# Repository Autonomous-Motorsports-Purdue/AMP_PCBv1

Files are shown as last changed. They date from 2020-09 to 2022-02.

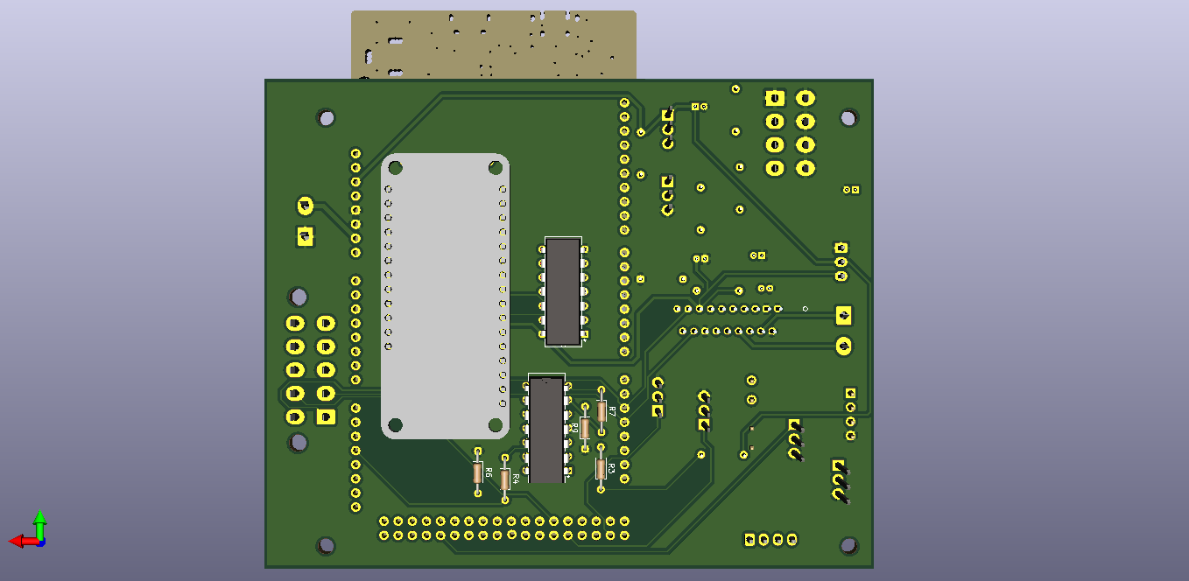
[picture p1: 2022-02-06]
PDF/PCB_2020_back.png

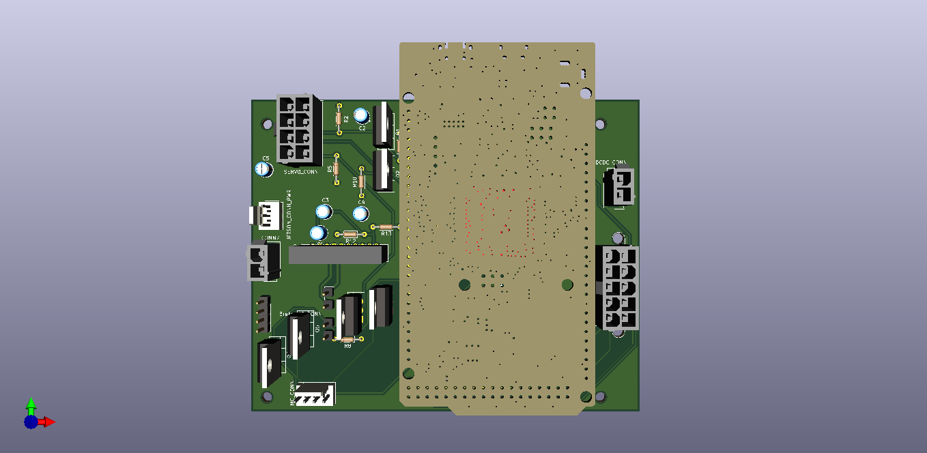
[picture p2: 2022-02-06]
PDF/PCB_2020.png

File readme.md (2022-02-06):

PCB Documentation

	- H-bridge
		- An H-bridge is made up of four MOSFETs and four diodes.
		- It switches motor direction based on which two MOSFETs are on.
		- The diodes serve to allow reverse current from the motor to be released.
		- The current solution is Adafruit DRV8871.
			- Its current Limit is 3.6 Amps.
			- This is not enough for the brake Linear Actuator.
		- Recommend switching from DRV8871 to MCP1407.
		- Has peak current capability of 6 A, which is enough for the braking actuator.
		- https://ww1.microchip.com/downloads/en/DeviceDoc/20002019C.pdf
			
	- Steering PWM
		- A square wave is sent to input A of the servo.
		- The pulse width determines position of servo.
		
	- Differential Amplifier 
		- 
		- The formula for a voltage divider is V = VR + (R3/R1)(V1 - V2).
		- The circuit amplifies the difference between the two inputs and adds the voltage VR as an offset.
		- Amplifier for PCB needs to change 0.55 V to 0 V, and  2.75 to 12 volts.
		- Diagram for Reference: https://www.electronicshub.org/wp-content/uploads/2015/01/1.-Differential-amplifier-circuit.jpg
		
	- Braking Linear Actuator
		- 5 Amp Max Current Draw at 12 Volts
		- Duty Cycle: 5 minutes on, 15 minutes off
		- Speed of 1.38 in/s with load of 35 lbs

		Changes
			-C1, C3, C4 backwards footprints (non-polarized capacitors
			-Resistor footprints larger
			-

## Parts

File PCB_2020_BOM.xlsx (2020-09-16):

Reference | Quantity | Value | Footprint | Datasheet | Additional Connector | Crimp Terminal
C2 C3 C4 C5 C1 | 5 | 0.1uF | Capacitor_SMD:C_0805_2012Metric_Pad1.15x1.40mm_HandSolder | https://www.digikey.com/product-detail/en/samsung-electro-mechanics/CL21B104JBCNNNC/1276-1090-1-ND/3889176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
CONN1 | 1 | FTDI | Drivetrain_control:FTDI_CONN | https://www.digikey.com/product-detail/en/sparkfun-electronics/BOB-13263/1568-1720-ND/7675364
CONN2 | 1 | SERVO_CONN | Connector_Molex:Molex_Mini-Fit_Jr_5566-08A2_2x04_P4.20mm_Vertical | https://www.molex.com/molex/products/datasheet.jsp?part=active/0039288080_PCB_HEADERS.xml | https://www.molex.com/molex/products/datasheet.jsp?part=active/0039012085_CRIMP_HOUSINGS.xml | https://www.molex.com/molex/products/datasheet.jsp?part=active/0039000038_CRIMP_TERMINALS.xml
CONN3 | 1 | DCDC_CONN | Connector_Molex:Molex_Mini-Fit_Jr_5566-02A_2x01_P4.20mm_Vertical | https://www.molex.com/molex/products/datasheet.jsp?part=active/0039288020_PCB_HEADERS.xml | https://www.molex.com/molex/products/datasheet.jsp?part=active/0039012025_CRIMP_HOUSINGS.xml | https://www.molex.com/molex/products/datasheet.jsp?part=active/0039000038_CRIMP_TERMINALS.xml
CONN4 | 1 | JETSON_CONN_PWR | Connector_Molex:Molex_KK-254_AE-6410-03A_1x03_P2.54mm_Vertical | https://www.molex.com/molex/products/datasheet.jsp?part=active/0022272031_PCB_HEADERS.xml | https://www.molex.com/molex/products/datasheet.jsp?part=active/0022012037_CRIMP_HOUSINGS.xml | https://www.molex.com/molex/products/datasheet.jsp?part=active/0008500113_CRIMP_TERMINALS.xml
CONN5 | 1 | MC_CONN | Connector_Molex:Molex_KK-254_AE-6410-04A_1x04_P2.54mm_Vertical | https://www.molex.com/molex/products/datasheet.jsp?part=active/0022272041_PCB_HEADERS.xml | https://www.molex.com/molex/products/datasheet.jsp?part=active/0022012047_CRIMP_HOUSINGS.xml | https://www.molex.com/molex/products/datasheet.jsp?part=active/0008500113_CRIMP_TERMINALS.xml
CONN6 | 1 | Brake_MC_CONN | Drivetrain_control:Brake_MC_Conn | https://cdn-shop.adafruit.com/product-files/3190/drv8871.pdf | https://learn.adafruit.com/adafruit-drv8871-brushed-dc-motor-driver-breakout/
CONN7 | 1 | Brake_CONN | Connector_Molex:Molex_KK-254_AE-6410-02A_1x02_P2.54mm_Vertical | https://www.molex.com/molex/products/datasheet.jsp?part=active/0022272021_PCB_HEADERS.xml | https://www.molex.com/molex/products/datasheet.jsp?part=active/0022012027_CRIMP_HOUSINGS.xml | https://www.molex.com/molex/products/datasheet.jsp?part=active/0008500113_CRIMP_TERMINALS.xml
IC1 | 1 | LM358N | Package_DIP:DIP-8_W7.62mm_Socket | https://www.digikey.com/product-detail/en/texas-instruments/LM358N-NOPB/LM358NNS-NOPB-ND/6264 | https://www.digikey.com/product-detail/en/3m/4808-3004-CP/3M5473-ND/1133626
Q1 Q7 Q8 | 1 | 220mA/50V/3.5Î© | Package_TO_SOT_SMD:SOT-23 | https://www.digikey.com/product-detail/en/on-semiconductor/BSS138-F085/BSS138-F085OSCT-ND/9086388
Q3 Q2 Q4 Q5 Q6 | 5 | 100V/17A | Package_TO_SOT_THT:TO-220-3_Vertical | https://www.infineon.com/dgdl/irl530npbf.pdf?fileId=5546d462533600a40153565fad5c2560
R1 R2 R6 R8 R7 R9 | 6 | 10k | Resistor_SMD:R_0805_2012Metric_Pad1.15x1.40mm_HandSolder
R3 | 1 | 3k | Resistor_SMD:R_0805_2012Metric_Pad1.15x1.40mm_HandSolder
R4 | 1 | 6.8k | Resistor_SMD:R_0805_2012Metric_Pad1.15x1.40mm_HandSolder
R5 R18 | 2 | 560 | Resistor_SMD:R_0805_2012Metric_Pad1.15x1.40mm_HandSolder
U1 | 1 | TI_CONN | Drivetrain_control:TI_Footprint | https://www.digikey.com/product-detail/en/te-connectivity-amp-connectors/826629-2/A105107-ND/1130753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

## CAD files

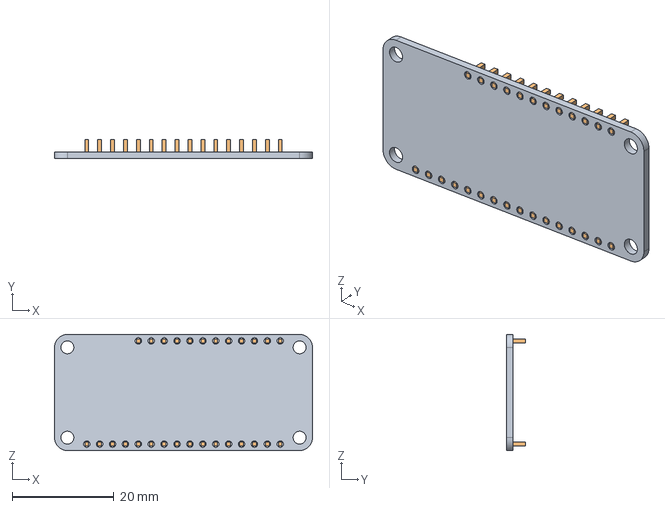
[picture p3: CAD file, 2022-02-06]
Resources/3D Models/Feather v1.iges
50.8 x 3.81 x 22.9 mm

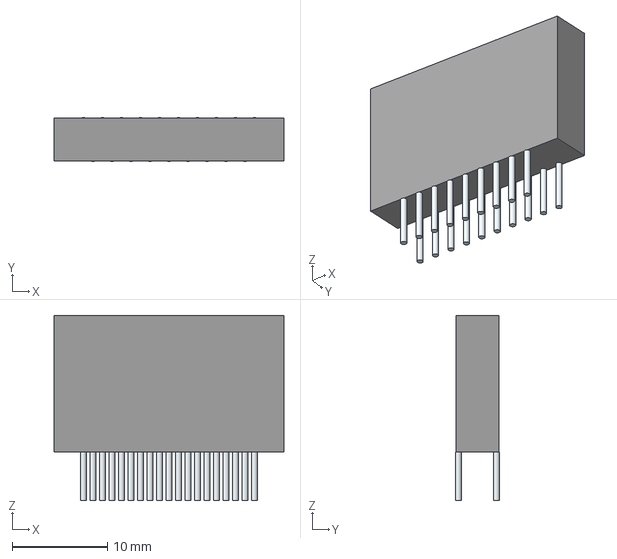
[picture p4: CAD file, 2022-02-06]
Resources/3D Models/STK681-332-E.stp
24.2 x 4.64 x 19.5 mm
Leads

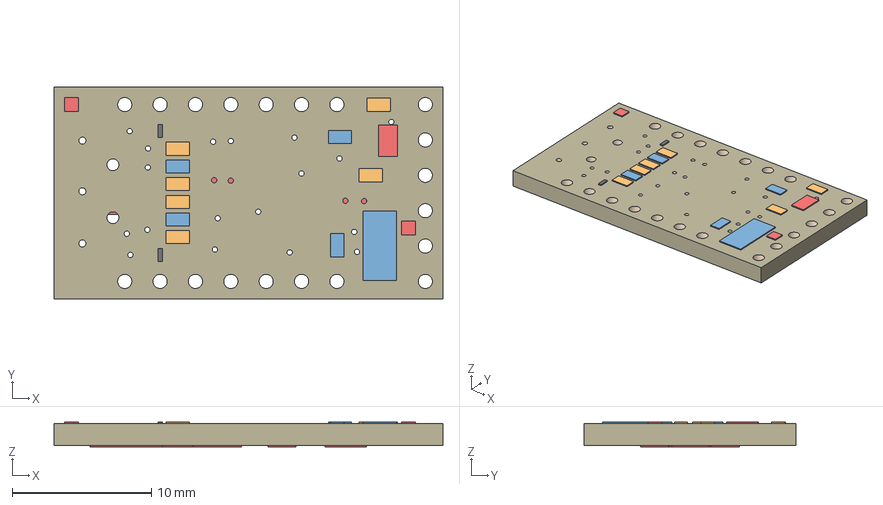
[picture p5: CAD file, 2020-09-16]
Resources/3D Models/ft231x-breakout-v11 v2.step
27.9 x 15.2 x 1.77 mm
Board
0.1uF x 4
1K x 4
SJ_3
10uF
Yellow x 2
TXLED
RXLED
2N7002PW
10k x 2
OSHW-LOGOS
FIDUCIAL1X2 x 2
SFE_LOGO_NAME.1_INCH

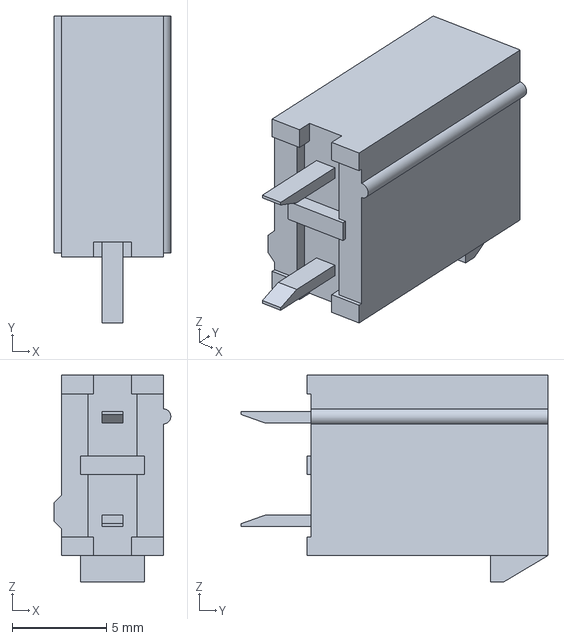
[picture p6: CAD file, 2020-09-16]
Resources/3D Models/Molex_Mini_Fit_Jr_1x2.stp
6.20 x 16.3 x 11.0 mm

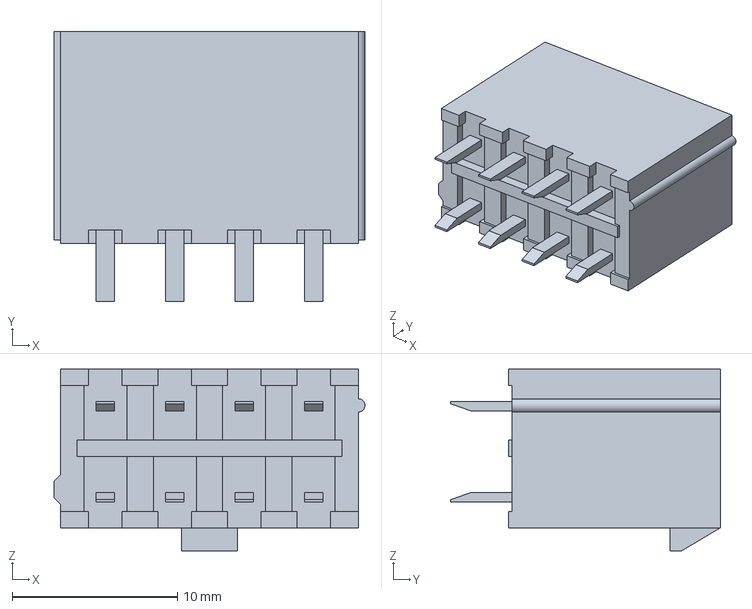
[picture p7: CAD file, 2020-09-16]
Resources/3D Models/Molex_Mini_Fit_Jr_2x4.stp
18.8 x 16.3 x 11.0 mm

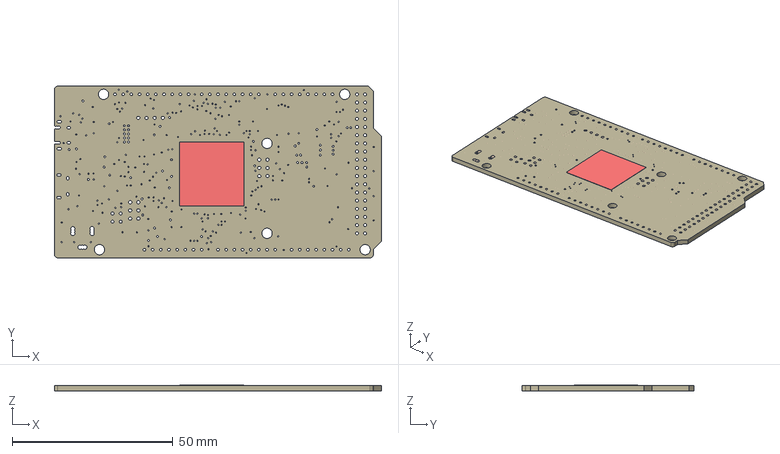
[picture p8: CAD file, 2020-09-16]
Resources/3D Models/DUE_V02g v1.step
101.6 x 53.3 x 1.77 mm
Board
ATSAM3X8EA-AU

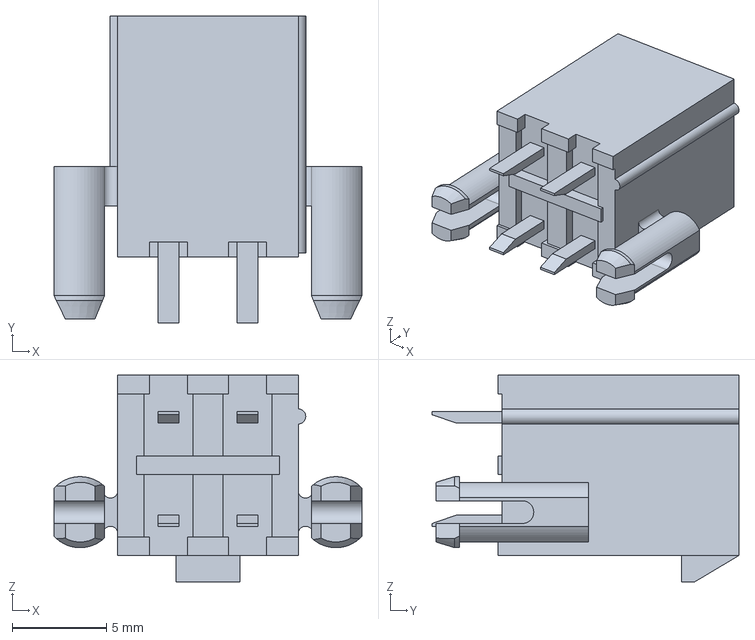
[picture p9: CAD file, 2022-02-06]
Resources/3D Models/39299047.stp
16.4 x 16.3 x 11.0 mm

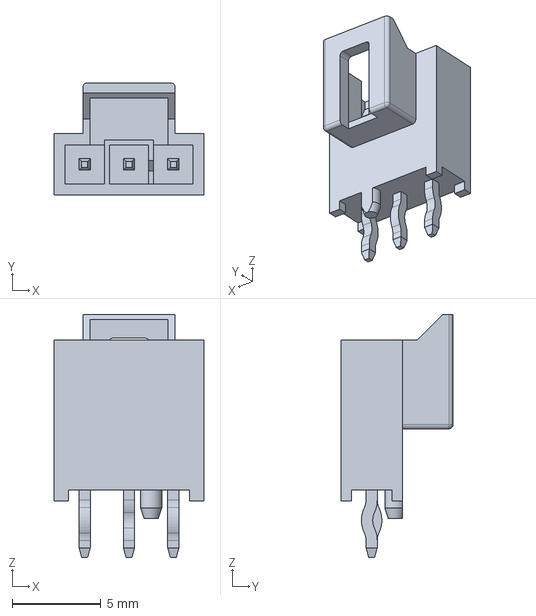
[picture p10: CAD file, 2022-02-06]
Resources/3D Models/1053091103.stp
8.44 x 6.34 x 13.7 mm

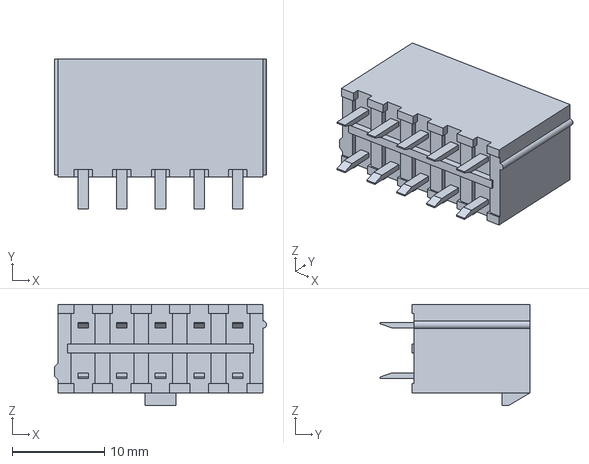
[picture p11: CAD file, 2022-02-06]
Resources/3D Models/39281103.stp
23.0 x 16.3 x 11.0 mm

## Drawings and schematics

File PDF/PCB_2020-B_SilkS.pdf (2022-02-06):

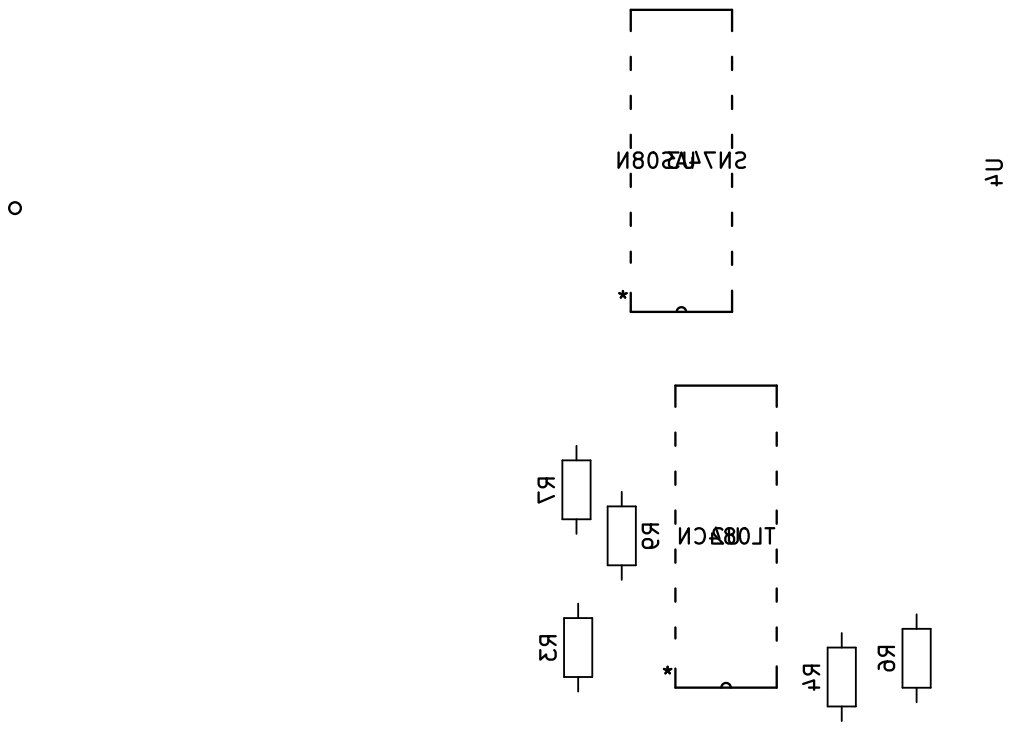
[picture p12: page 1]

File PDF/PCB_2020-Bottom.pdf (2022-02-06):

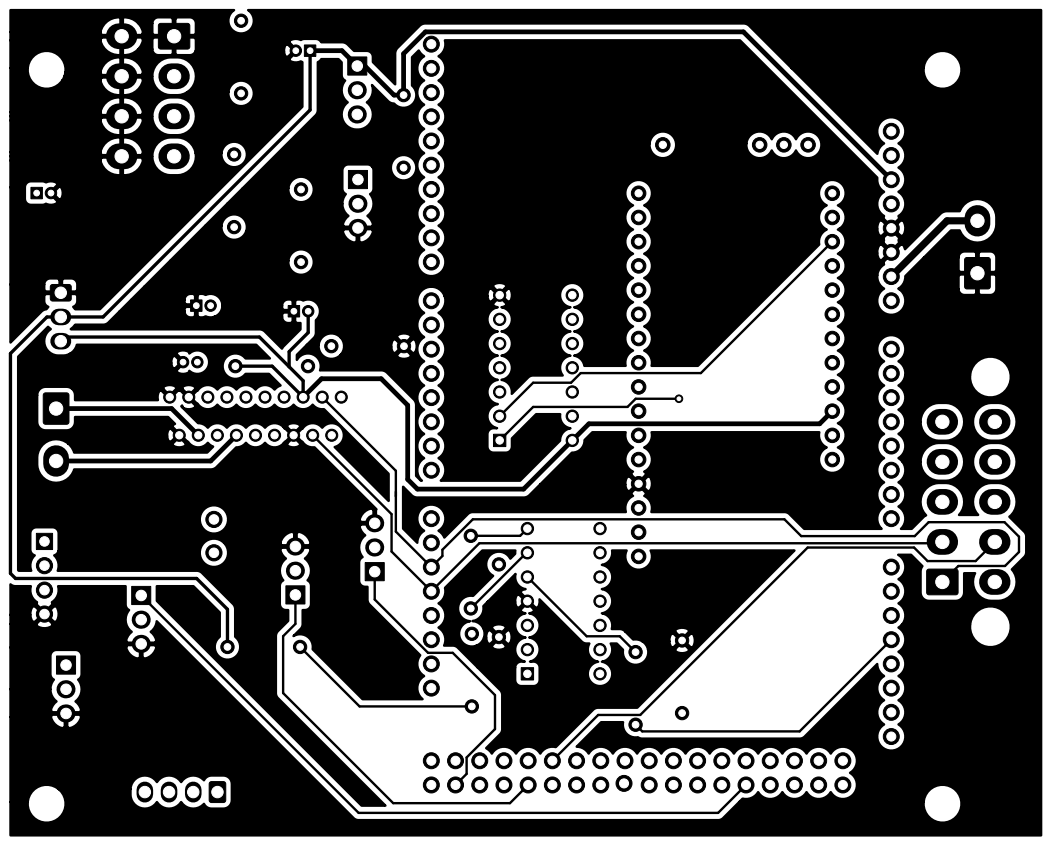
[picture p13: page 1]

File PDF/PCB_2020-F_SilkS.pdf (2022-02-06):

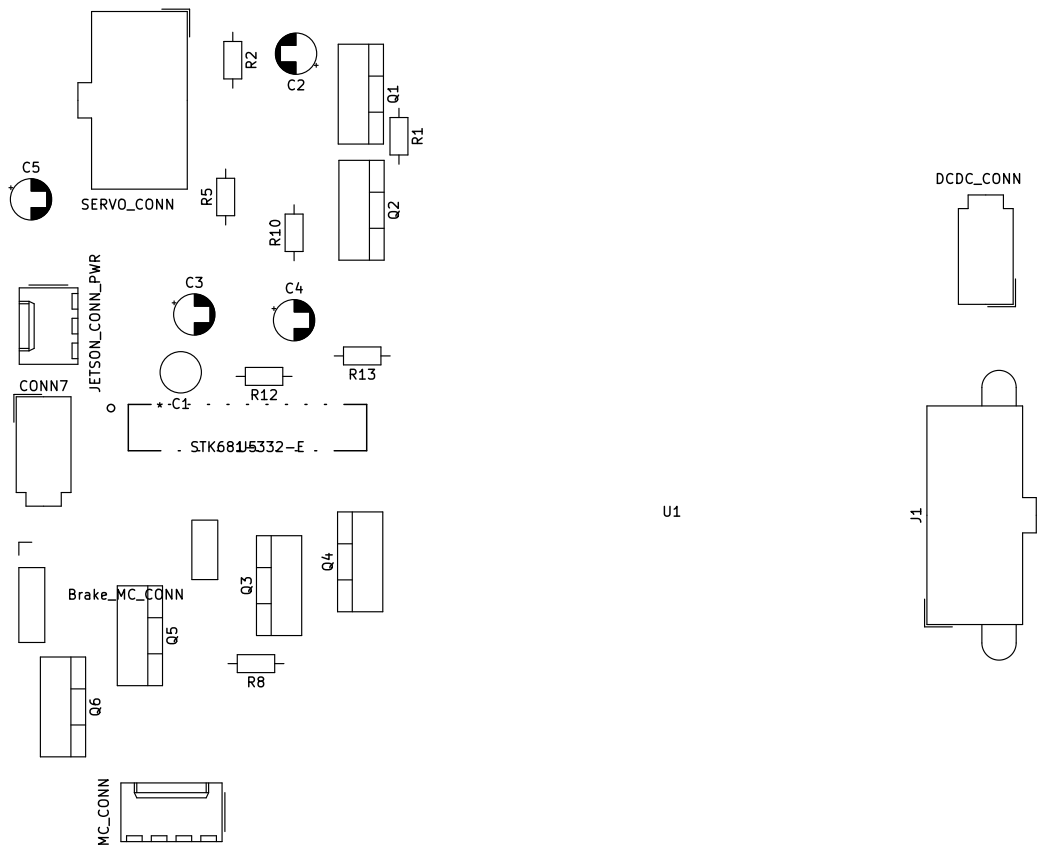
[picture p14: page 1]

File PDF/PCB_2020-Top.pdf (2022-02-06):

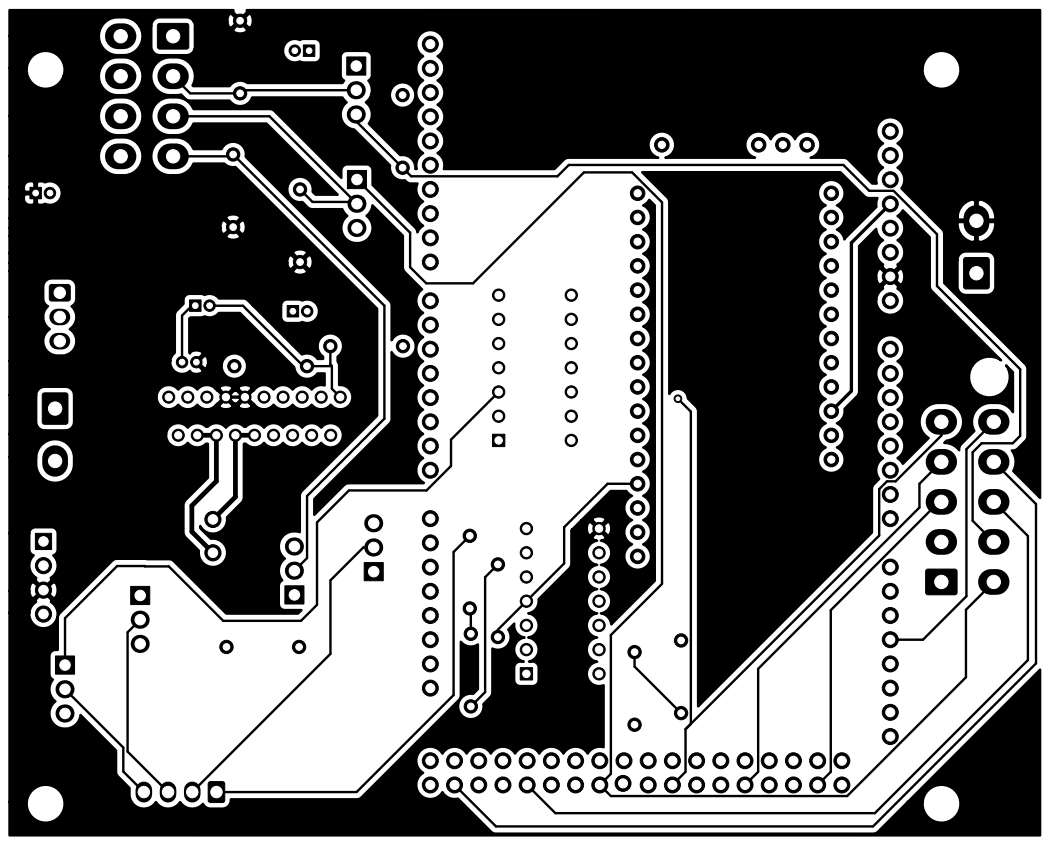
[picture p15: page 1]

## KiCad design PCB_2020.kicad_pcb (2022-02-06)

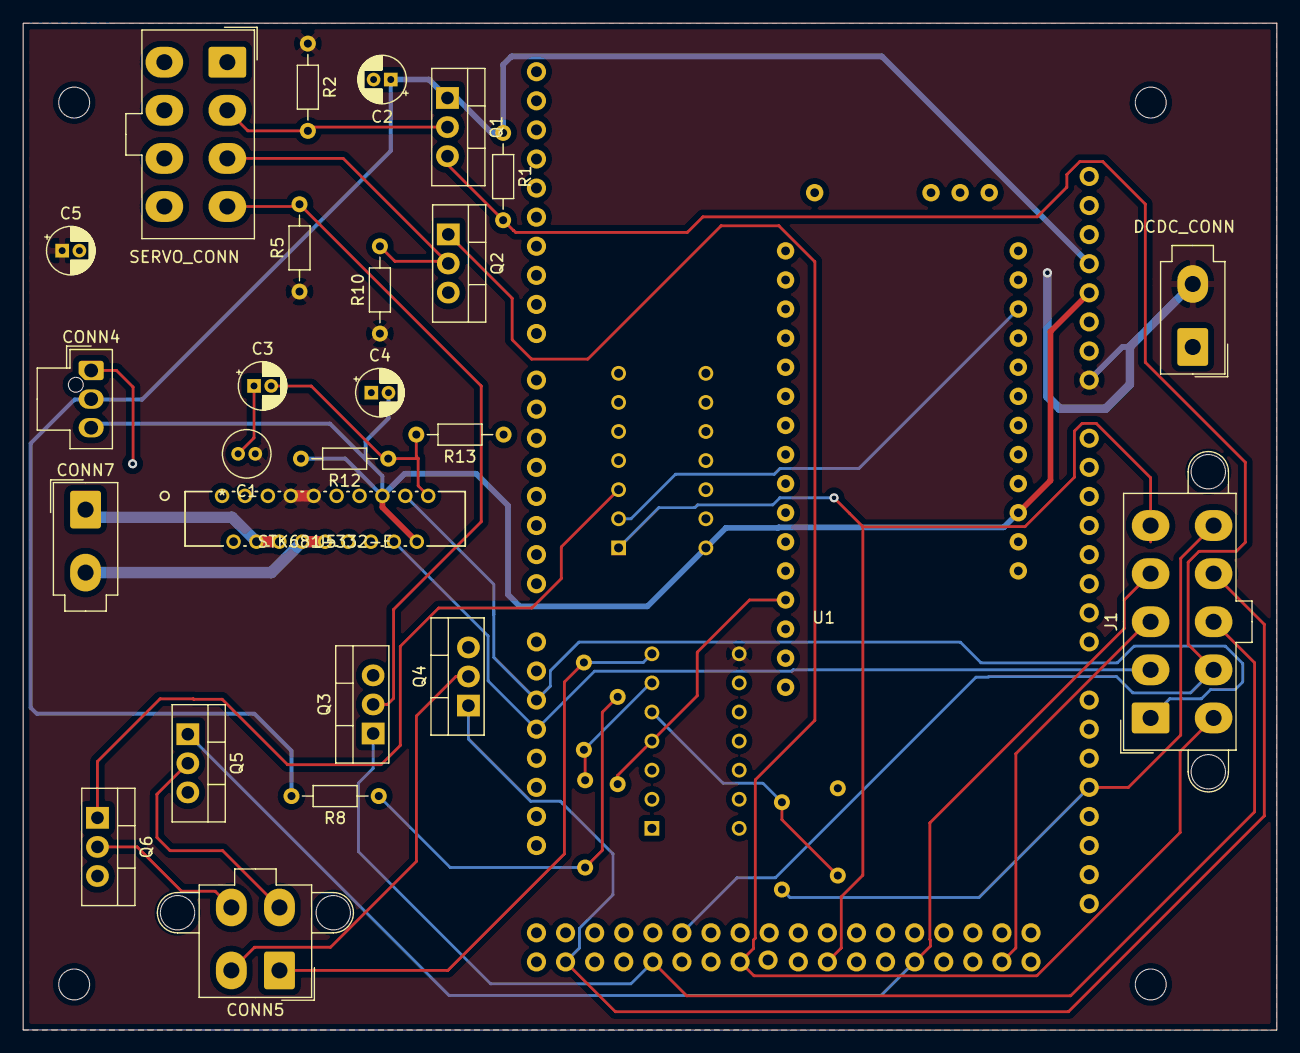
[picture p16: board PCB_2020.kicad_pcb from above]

Board: 2 copper layers, 109.5 x 87.9 mm, 38 parts (0 on the bottom side), 29 nets.

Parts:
C1: 47u; C_Radial_D4.0mm_H5.0mm_P1.50mm
C2, C5: 0.1uF; CP_Radial_D4.0mm_P1.50mm
C3: 0.1u; CP_Radial_D4.0mm_P1.50mm
C4: 10u; CP_Radial_D4.0mm_P1.50mm
CONN2: SERVO_CONN; Molex_Mini-Fit_Jr_5566-08A_2x04_P4.20mm_Vertical
CONN3: DCDC_CONN; Molex_Mini-Fit_Jr_5566-02A_2x01_P4.20mm_Vertical
CONN4: JETSON_CONN_PWR; Molex_Nano-Fit_105309-xx03_1x03_P2.50mm_Vertical
CONN5: MC_CONN; Molex_Mini-Fit_Jr_5566-04A2_2x02_P4.20mm_Vertical
CONN7: Brake_CONN; Molex_Mini-Fit_Jr_5566-02A_2x01_P4.20mm_Vertical
H1, H2, H3, H4: MountingHole; MountingHole_2.7mm
J1: Conn_01x10_Female; Molex_Mini-Fit_Jr_5566-10A2_2x05_P4.20mm_Vertical
Q1, Q2, Q3, Q4, Q5, Q6: 100V/17A; TO-220-3_Vertical
R1, R2: 10k; R_Axial_DIN0204_L3.6mm_D1.6mm_P7.62mm_Horizontal
R3, R4, R9: 1000; R_Axial_DIN0204_L3.6mm_D1.6mm_P7.62mm_Horizontal
R5, R10: 560; R_Axial_DIN0204_L3.6mm_D1.6mm_P7.62mm_Horizontal
R6, R7: 5400; R_Axial_DIN0204_L3.6mm_D1.6mm_P7.62mm_Horizontal
R8: 5000; R_Axial_DIN0204_L3.6mm_D1.6mm_P7.62mm_Horizontal
R12: 4k; R_Axial_DIN0204_L3.6mm_D1.6mm_P7.62mm_Horizontal
R13: 1k; R_Axial_DIN0204_L3.6mm_D1.6mm_P7.62mm_Horizontal
U1: AMP_DUE_SCH; Arduino DUE
U2: TL084CN
U3: SN74AS08N
U4: LoRa
U5: STK681-332-E

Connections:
+3V3: C2.1, CONN4.2, Q1.1, R1.1, R8.2, U1.4
+5V: C4.2, CONN4.3, R12.2, U1.5, U3.14, U4.55, U5.15, U5.18
+12V: C1.1, C5.1, CONN3.2, R2.1, R5.1, R10.1, U1.8, U2.8, U5.7, U5.9
/LAUNCHXL-F28379D Breakout/Brake_Out_1: CONN7.2, U5.8, U5.10
/LAUNCHXL-F28379D Breakout/Brake_Out_2: CONN7.1, U5.4, U5.6
/LAUNCHXL-F28379D Breakout/EN+: CONN2.4, Q3.2, R5.2
/LAUNCHXL-F28379D Breakout/FS1_MC: CONN5.4, Q6.2
/LAUNCHXL-F28379D Breakout/FWD_MC: CONN5.3, Q5.2
/LAUNCHXL-F28379D Breakout/INPUT_A+: CONN2.3, Q2.2, R10.2
/LAUNCHXL-F28379D Breakout/INPUT_B+: CONN2.2, Q1.2, R2.2
/LAUNCHXL-F28379D Breakout/REV_MC: CONN5.2, Q4.2
/LAUNCHXL-F28379D Breakout/THROTTLE_MC: CONN5.1, R7.1, U2.7
Brake_PWM_1: J1.2, U1.65, U5.16
Brake_PWM_2: J1.1, U1.66, U5.17
EN+_CTL: J1.8, Q3.1, U1.56
FS1_CTL: J1.5, U1.50, U3.1
FS1_RMT: Q6.1, U3.3
FWD_CTL: J1.4, Q5.1, U1.47
GND: C1.2, C2.2, C3.1, C4.1, C5.2, CONN2.1, CONN2.5, CONN2.6, CONN2.7, CONN2.8, CONN3.1, CONN4.1, Q2.3, Q3.3, Q4.3, Q5.3, Q6.3, R6.1, R9.1, R13.1, U1.6, U1.7, U2.4, U3.7, U4.49, U5.1, U5.2, U5.3, U5.14
INPUT_A+_CTL: J1.6, Q2.1, U1.53
KS1_CTL: J1.3, U1.44
unnamed: C3.2, R12.1, R13.2, U5.19
unnamed: R3.1, R7.2, U2.6
unnamed: R3.2, R8.1, R9.2
unnamed: R4.1, R6.2, U2.5
unnamed: U3.2, U4.24
REV_CTL: J1.9, Q4.1, U1.59
STEERING: J1.7, Q1.3, R1.2, U1.37
THROTTLE: J1.10, R4.2, U1.20

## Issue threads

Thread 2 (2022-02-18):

Reversed capacitor footprints

benjamin-owen, 2022-02-18:
Capacitors C1, C3, and C4 footprints are reversed on the PCB silkscreen (indicating reverse polarity).

Closed 2023-09-08.

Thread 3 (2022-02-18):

Resistor footprints too small

benjamin-owen, 2022-02-18:
Many of the resistor footprints are too narrow for a resistor to comfortably fit.

Closed 2023-09-08.

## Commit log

2020-09-20 Worked on H-Bridge and Linear Actuator
2020-09-23 Adding KiCad Tutorial and Updated Readme
    [Tutorial-B_Cu.gbr, Tutorial-B_Mask.gbr, Tutorial-B_Paste.gbr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]
2020-09-29 Working on Diff Amp Simulation in KiCad
    [Diff Simulator.kicad_pcb, Diff Simulator.sch]
2020-10-06 Working on KiCad Simulation
    [Diff Simulator.sch]
2020-10-06 Working on Diff Simulator
    [Diff Simulator.sch]
2020-10-10 Working on Diff Simulator Bugs
    [Diff Simulator.sch]
2020-10-10 Mitch updated diff amp sim files
    [Diff Simulator.sch]
2020-10-11 LTSpice Simulation
    [LAUNCHXL-F28379D_Breakout.sch, LAUNCHXL-F28379D_Headers.sch, PCB_2020.sch]
2020-10-13 LTSpice Simulation Finished
    [LAUNCHXL-F28379D_Breakout.sch, LAUNCHXL-F28379D_Headers.sch]
2020-10-13 updated pcb
    [LAUNCHXL-F28379D_Breakout.sch]
2020-10-19 Updating PCB
    [LAUNCHXL-F28379D_Breakout.sch, LAUNCHXL-F28379D_Headers.sch, PCB_2020.kicad_pcb]
2020-10-20 Reworked PCB
    [PCB_2020.kicad_pcb]
2020-11-11 Working on PCB Routing for LoRa
    [LAUNCHXL-F28379D_Breakout.sch, LAUNCHXL-F28379D_Headers.sch, PCB_2020.kicad_pcb]
2020-11-25 Updating PCB with LoRa
    [LAUNCHXL-F28379D_Breakout.sch, LAUNCHXL-F28379D_Headers.sch, PCB_2020.kicad_pcb]
2021-01-17 Added AND gate for Feather LoRa, and changed over to through hole components
    [LAUNCHXL-F28379D_Breakout.sch, LAUNCHXL-F28379D_Headers.sch, PCB_2020.kicad_pcb]
2021-03-25 updated PCB with bluetooth connector for arduino signals
    [LAUNCHXL-F28379D_Breakout.sch, LAUNCHXL-F28379D_Headers.sch, PCB_2020.kicad_pcb]
2021-09-20 'updated files'
    [PCB_2020.kicad_pcb]
2021-09-27 updated 3d models for pcb items
    [Feather v1.iges, PCB_2020.kicad_pcb, STK681-332-E.stp]
2021-09-27 updated pcb models
    [39281103.stp, PCB_2020.kicad_pcb]
2021-09-28 deleted tutorial folder
    [Tutorial-B_Cu.gbr, Tutorial-B_Mask.gbr, Tutorial-B_Paste.gbr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]
2021-10-18 updated trace width
    [LAUNCHXL-F28379D_Breakout.sch, LAUNCHXL-F28379D_Headers.sch, PCB_2020.kicad_pcb]
2021-10-18 updated motor driver connections
    [LAUNCHXL-F28379D_Breakout.sch, PCB_2020.kicad_pcb]
2021-10-18 updated design rules
    [PCB_2020.kicad_pcb]
2021-10-23 changed connectors to be all Molex
    [1053091103.stp, 39299047.stp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]

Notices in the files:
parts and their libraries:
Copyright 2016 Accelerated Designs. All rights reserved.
